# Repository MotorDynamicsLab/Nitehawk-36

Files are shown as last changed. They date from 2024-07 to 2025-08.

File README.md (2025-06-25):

# Nitehawk-36

Nitehawk-36 is a toolboard featuring RP2040 MCU, TMC2209 stepper drive, ADXL345 accelerometer, and USB port. Nitehawk-36's USB based connection method allows for a simple and easy setup compared to other CAN toolboards. The USB connnection also allows for a secondary USB port to connect your nozzle webcam or eddy current probe.

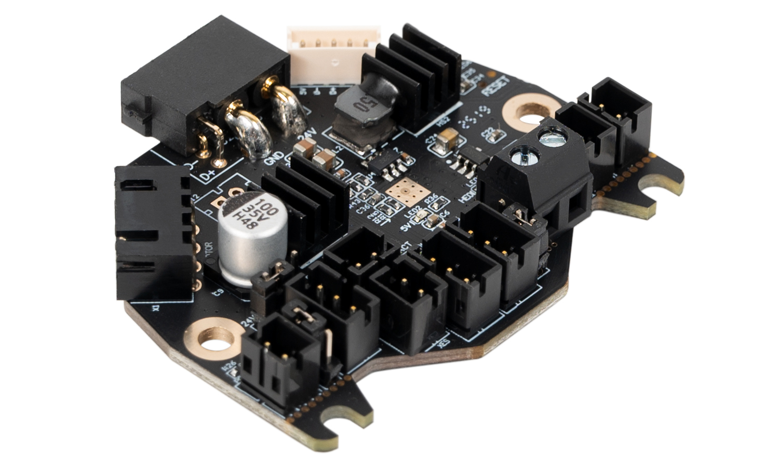
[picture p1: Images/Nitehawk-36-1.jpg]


# Features:

- Convenient wiring, no more complicated and error prone breakout cables
- USB Klipper connection, no additional software or hardware setup compared to CAN.
- Secondary USB port, an onboard USB port allows you to connect a second USB - device to your toolhead without running an additional umbilical cable.
- Custom toolhead cable, a single combined USB data and power cable rated for drag chain use, but can also be used in umbilical configuration.
- Convenient Input Shaping, run input shaper calibration at anytime with an onboard accelerometer.
- Tacho enabled HEF, the hotend fan port is three pin tachometer compatible, allowing for additional diagnostics and safety.

# Mount Guide
[Nitehawk 36 Universal Mount Guide](../master/STLs/Universal_Mount/NiteHawk%2036%20Mount.pdf)

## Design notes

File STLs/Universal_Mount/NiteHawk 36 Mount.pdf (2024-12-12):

# NiteHawk 36

## Universal Mount

# Mounts and Motor Adapter

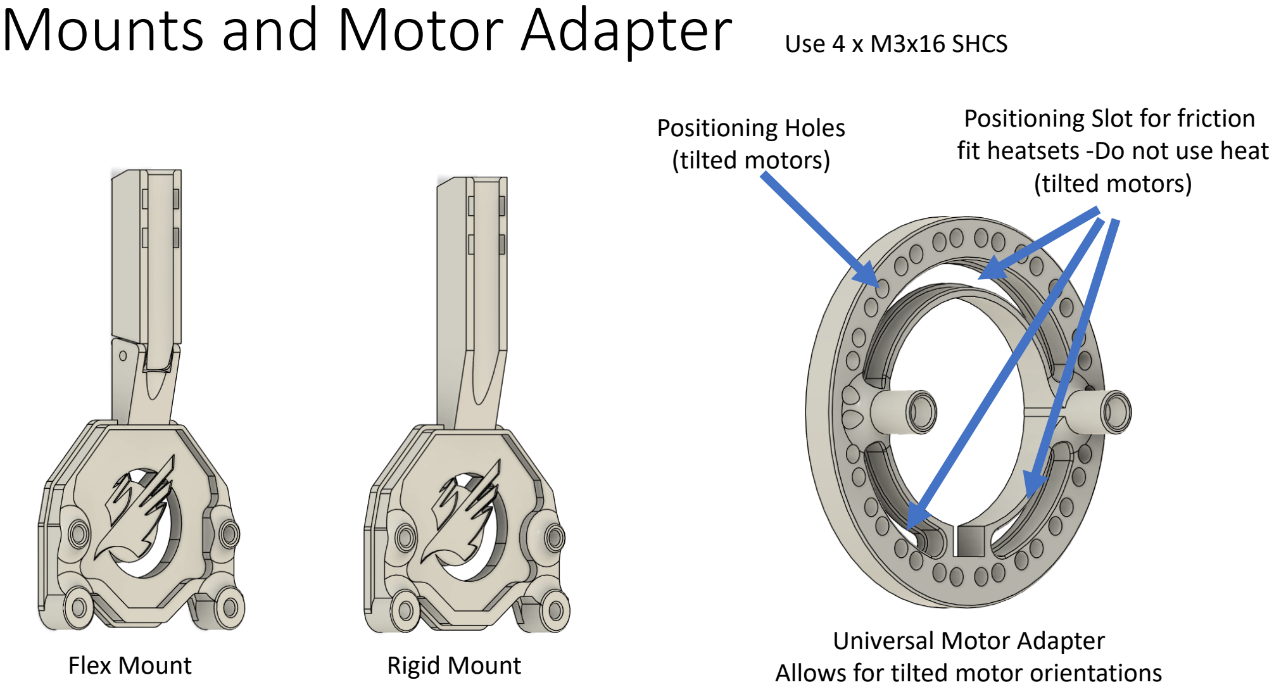
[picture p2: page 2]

Flex Mount | Rigid Mount

Universal Motor Adapter
Allows for tilted motor orientations

Positioning Slot for friction fit heatsets -Do not use heat (tilted motors)

Positioning Holes
(tilted motors)

Use 4 x M3x16 SHCS

# Flex Mount Prep

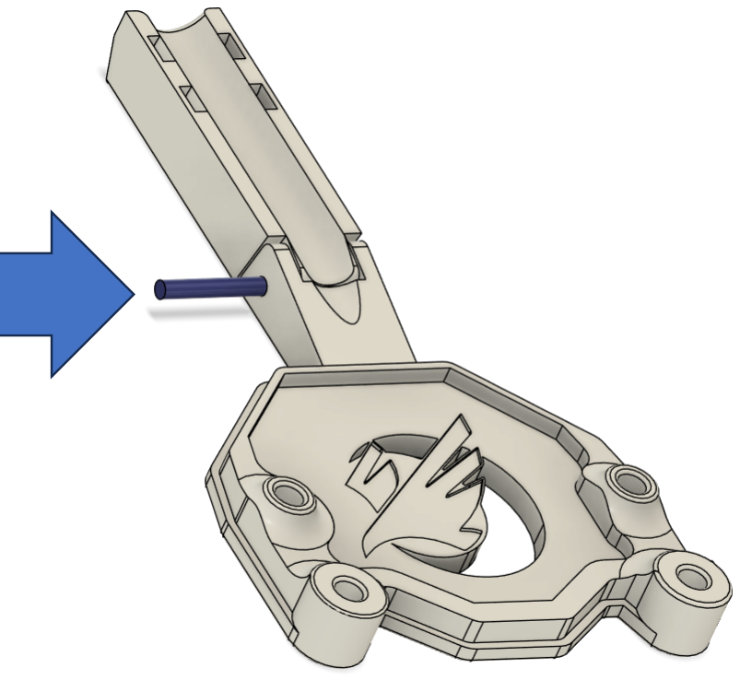
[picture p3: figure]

Cut a piece of filament slightly longer than the wide of the strain relief. Insert a piece of filament as a hinge. Melt the ends so the filament stay in place with a soldering iron.

# Flex and Rigid Mount Prep

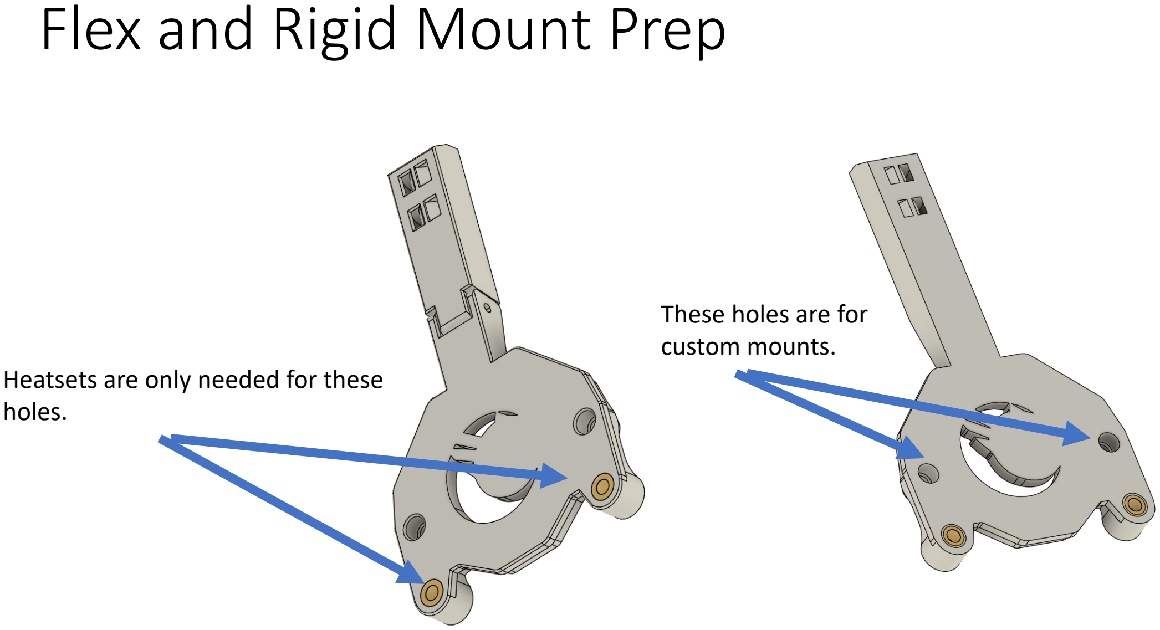
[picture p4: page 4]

Heatsets are only needed for these holes.

These holes are for
custom mounts.

# Extruders with Aligned Motor

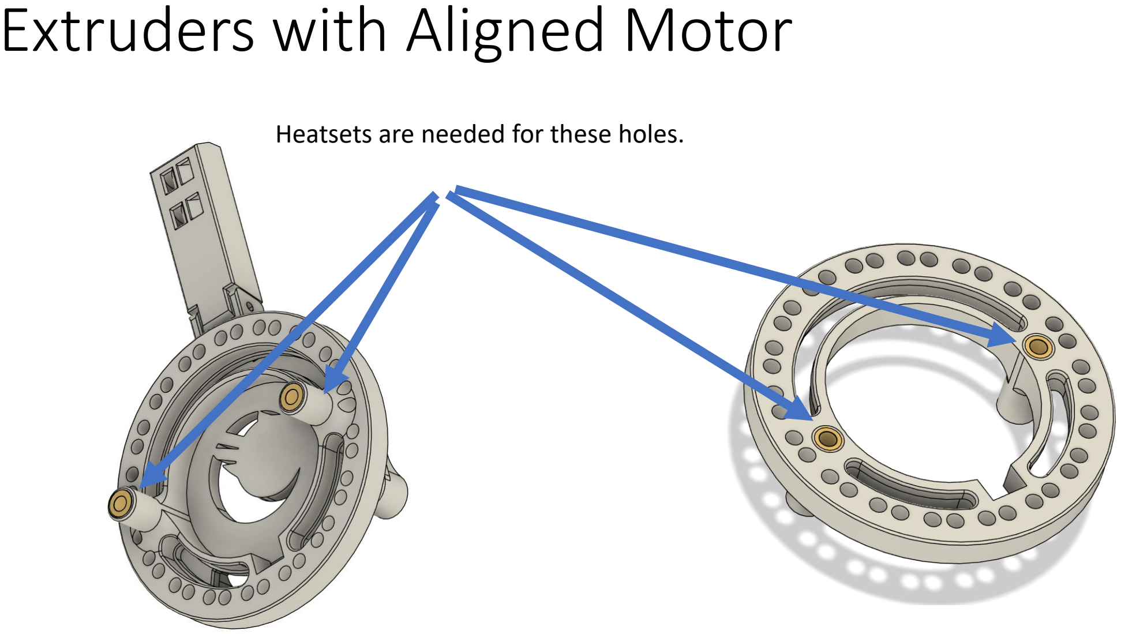
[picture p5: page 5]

Heatsets are needed for these holes.

# Extruders with Tilted Motor

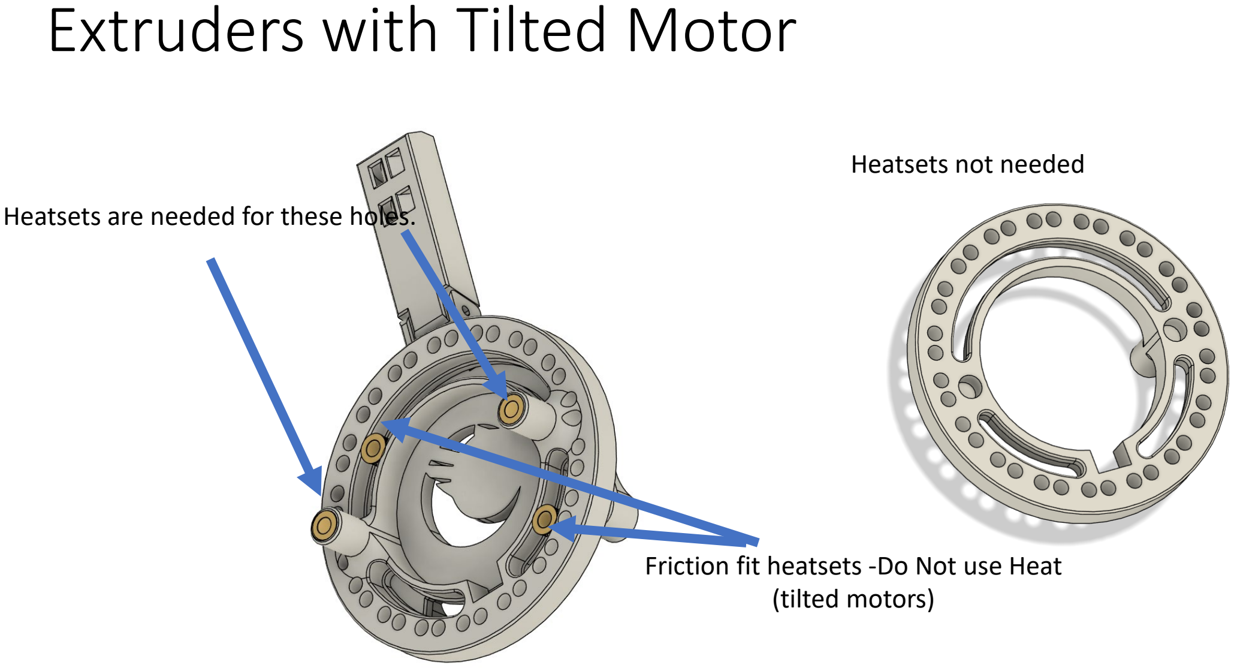
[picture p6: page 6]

Friction fit heatsets -Do Not use Heat (tilted motors)

Heatsets not needed
Heatsets are needed for these holes.

# Securing the NH36 Board

1. Use 2x M3x16 SHCS thread into plastic Do NOT overtighten

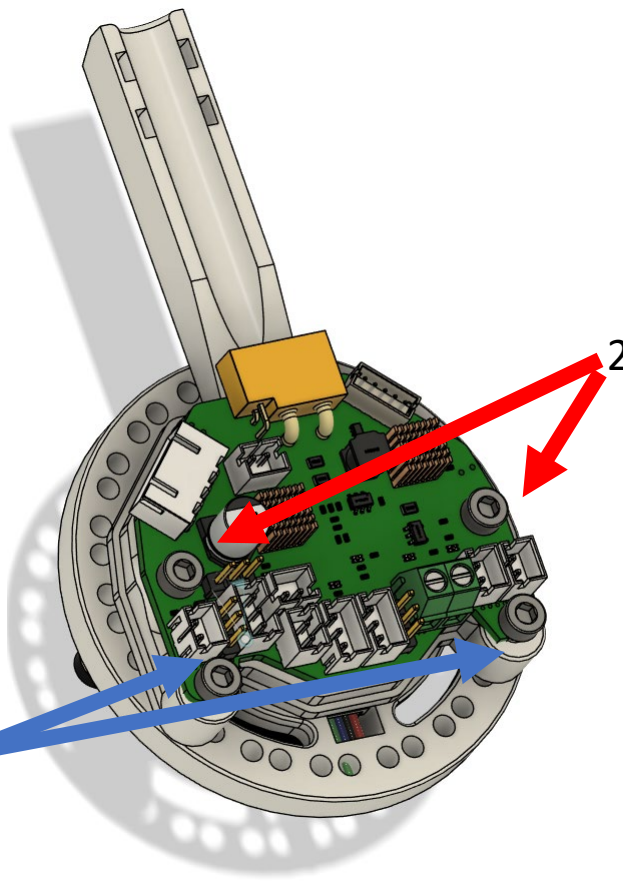
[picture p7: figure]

2.Use 2x M3x16 SHCS into friction fit heatsets

# Example

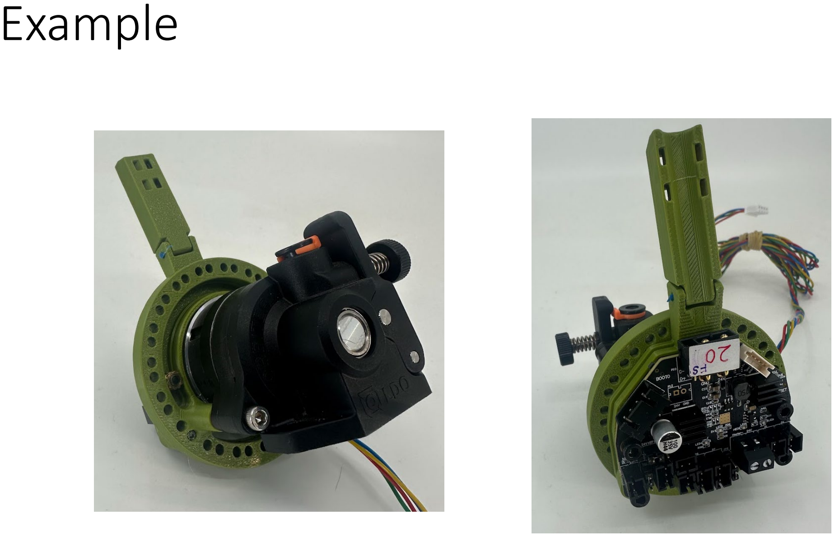
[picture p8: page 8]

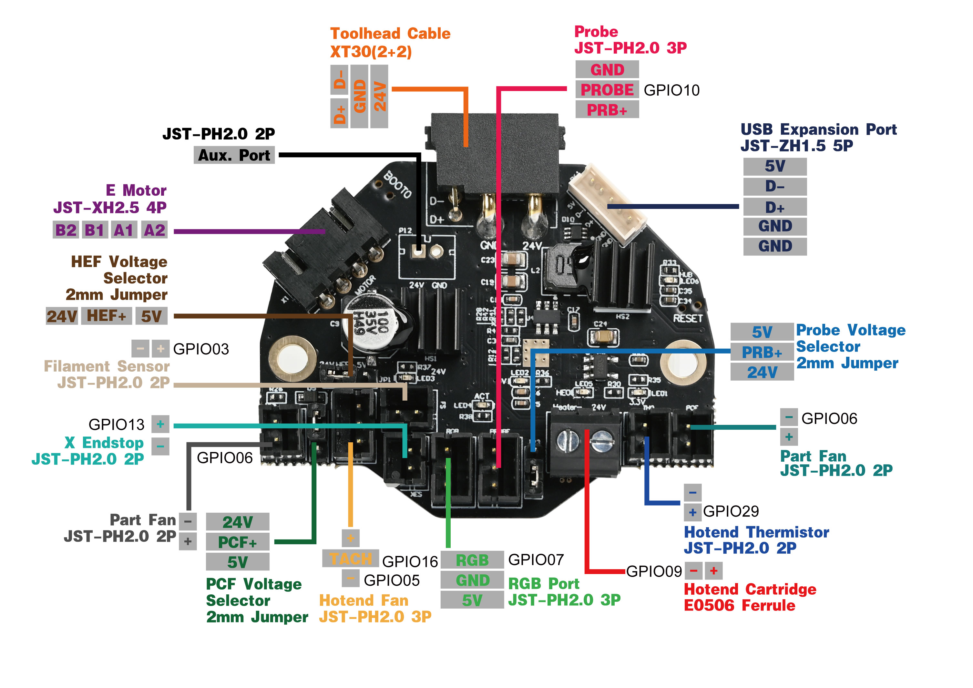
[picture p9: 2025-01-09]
Images/nh36_pcb_pinout.jpg

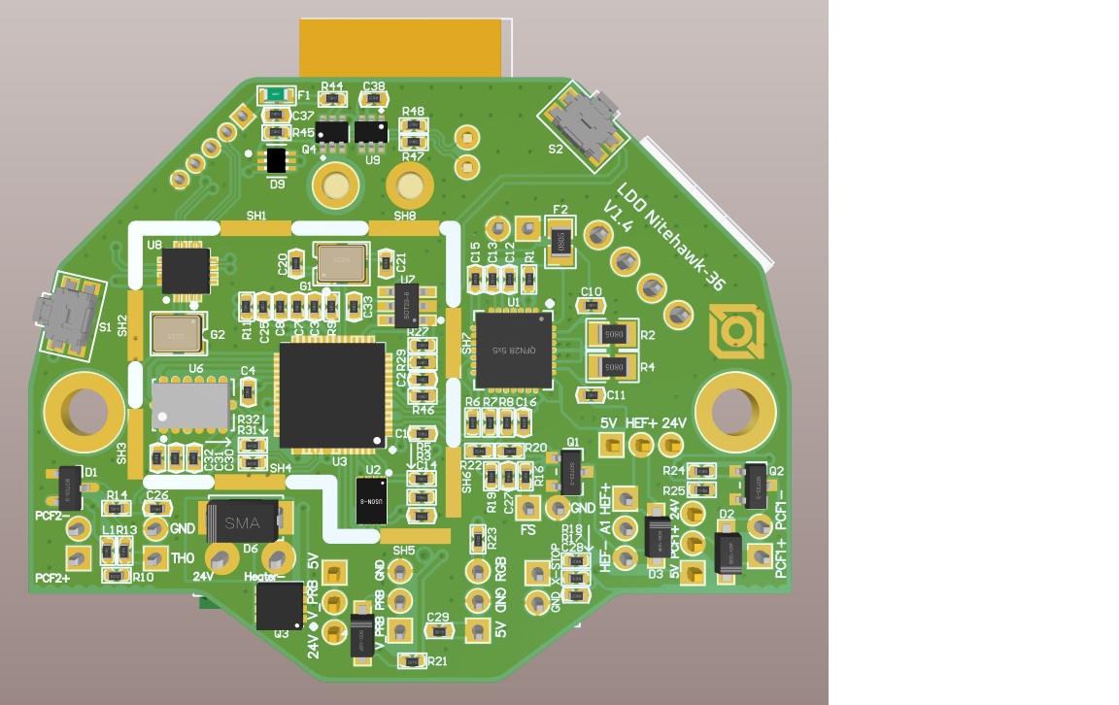
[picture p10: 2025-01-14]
Hardware/Nitehawk-36 V1.4/Nitehawk-36_V1.4 3D Layout Bottom.jpg

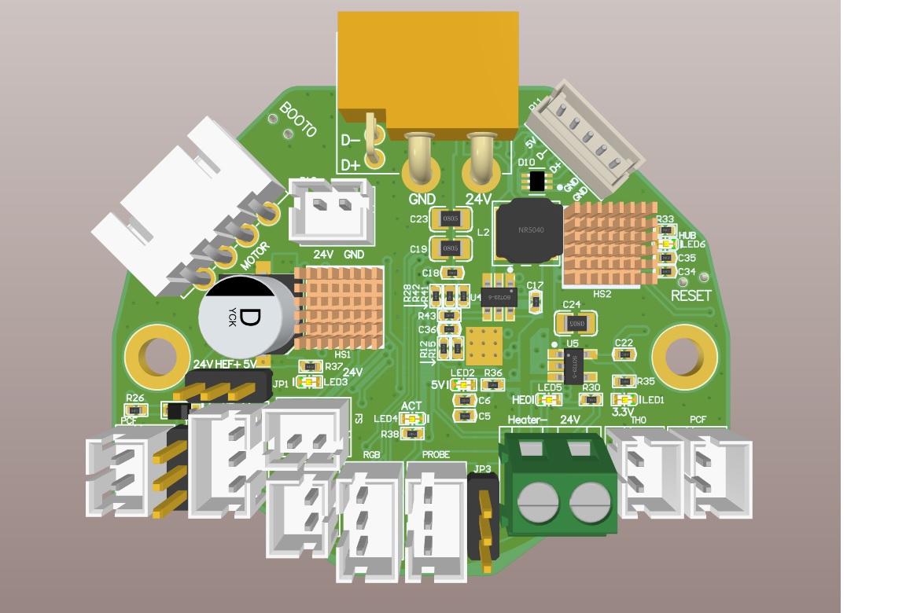
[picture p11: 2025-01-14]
Hardware/Nitehawk-36 V1.4/Nitehawk-36_V1.4 3D Layout Top.jpg

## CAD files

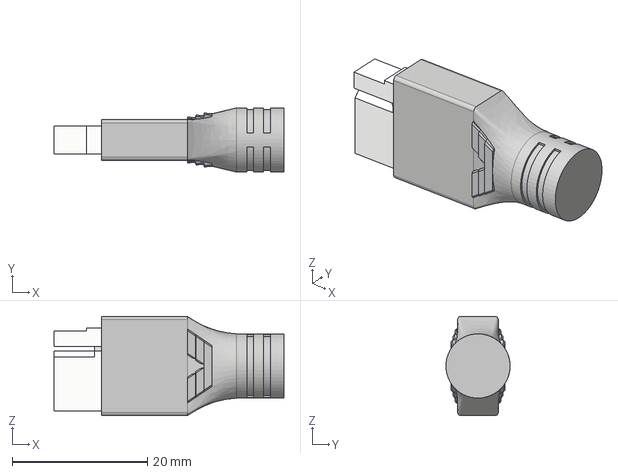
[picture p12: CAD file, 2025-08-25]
CAD/Umbilical_Overmold.step
34.0 x 9.50 x 14.7 mm
Connector
Overmold

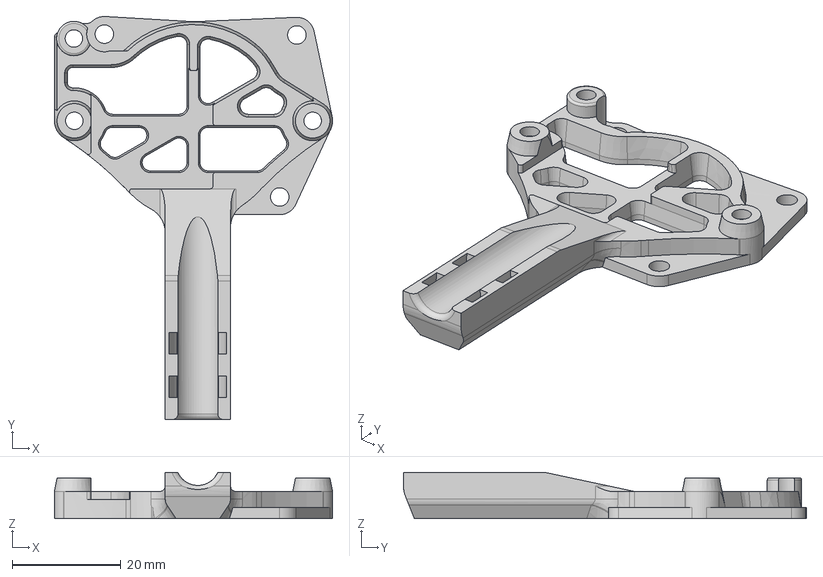
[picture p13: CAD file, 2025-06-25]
STLs/G2SA_WWG2_Mounts/NH36_v2_mount_WWG2.step
51.2 x 74.1 x 8.50 mm

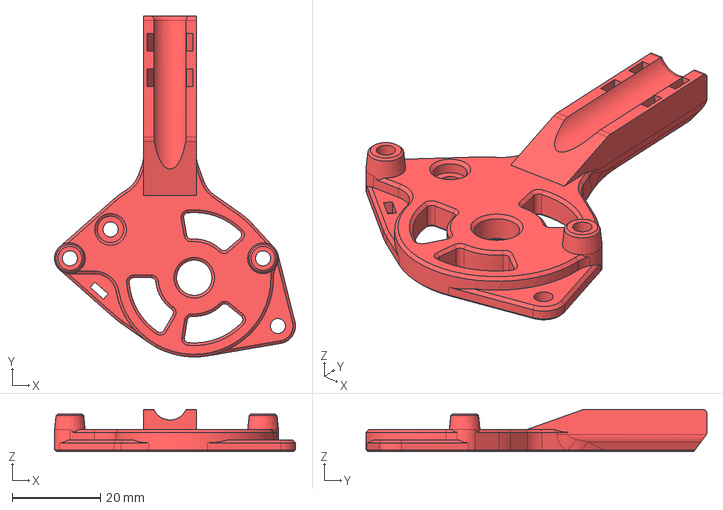
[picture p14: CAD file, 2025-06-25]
STLs/Generic_O2_Mount/NH36_O2_mount.step
54.7 x 77.4 x 9.60 mm

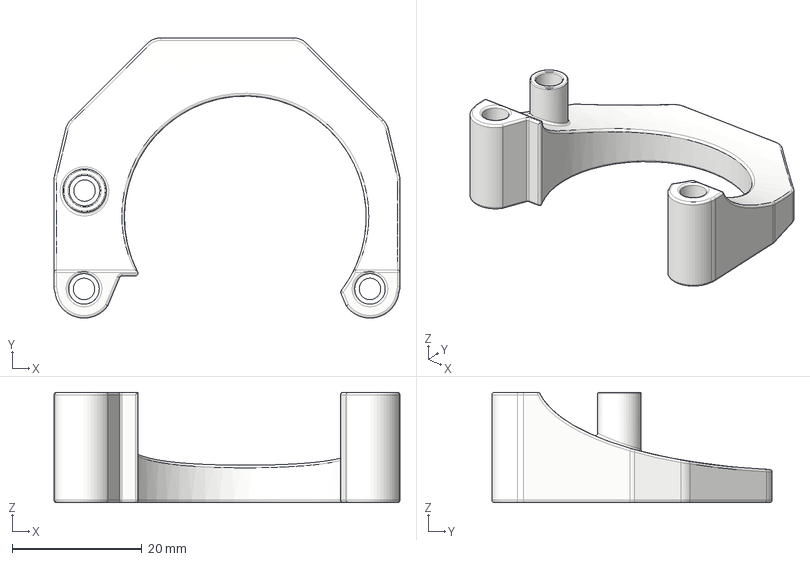
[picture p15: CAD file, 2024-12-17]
STLs/Universal_Mount/OrbiterMount.step
53.2 x 43.1 x 17.0 mm

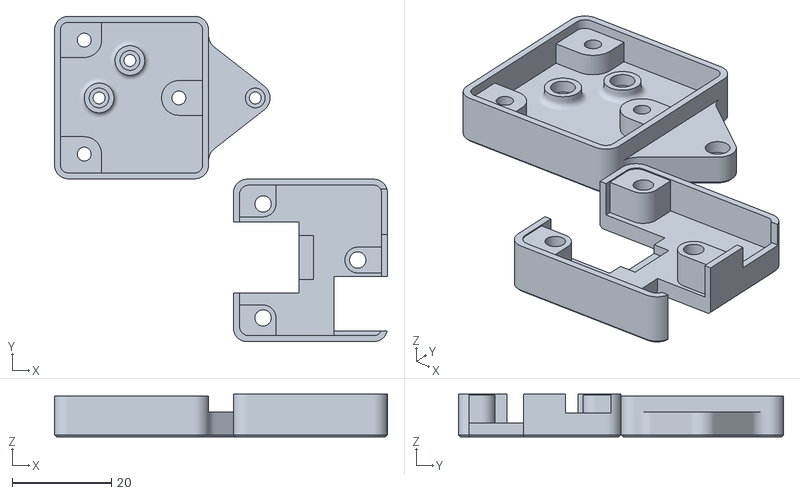
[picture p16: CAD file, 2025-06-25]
STLs/usb_adapter_mount_narrow.stl
67.2 x 65.6 x 8.60

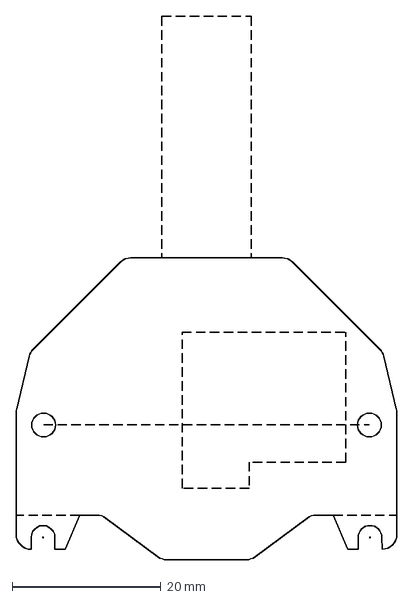
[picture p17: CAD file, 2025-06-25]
CAD/NH36-outline.dxf
51.2 x 73.1 mm

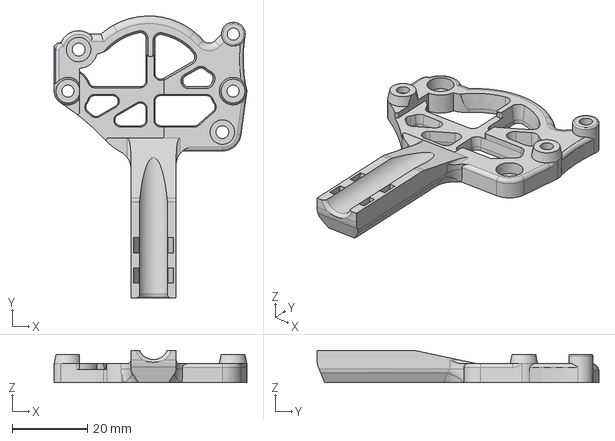
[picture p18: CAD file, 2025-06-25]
STLs/G2SA_WWG2_Mounts/NH36_v2_mount_G2SA.step
51.2 x 74.9 x 8.50 mm

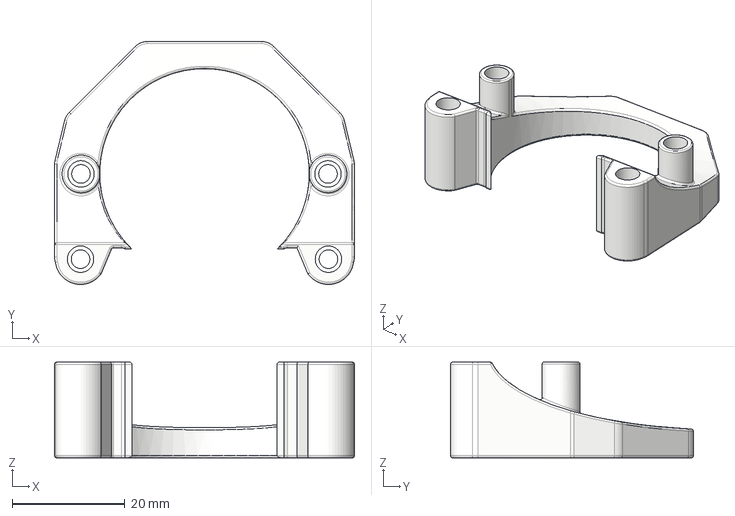
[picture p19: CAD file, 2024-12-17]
STLs/Universal_Mount/StandardMount.step
53.2 x 43.1 x 17.0 mm

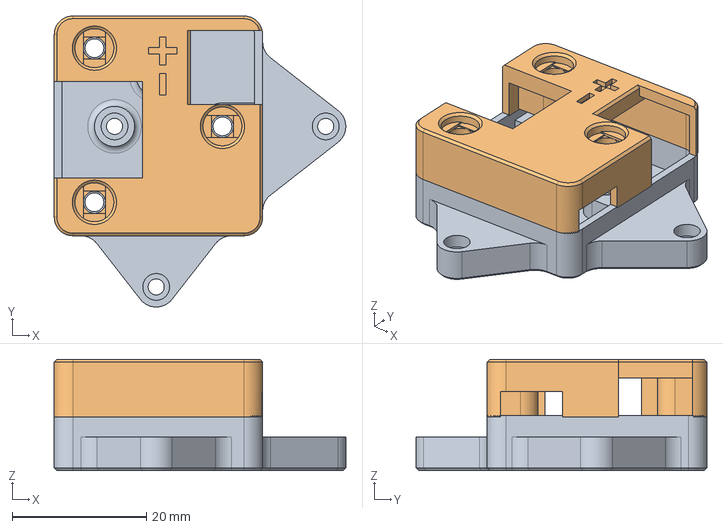
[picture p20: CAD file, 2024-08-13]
STLs/usb_adapter_mount.step
43.5 x 43.4 x 16.6 mm
Mount
Cover

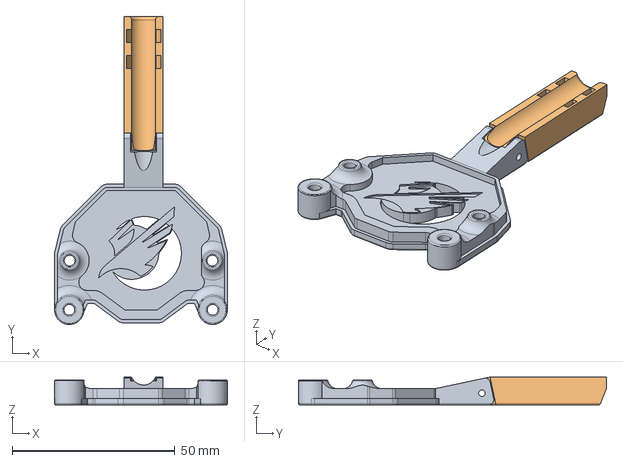
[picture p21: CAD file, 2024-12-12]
STLs/Universal_Mount/NH36_Flex_Mount.step
53.2 x 94.6 x 8.50 mm
Mount
Strain

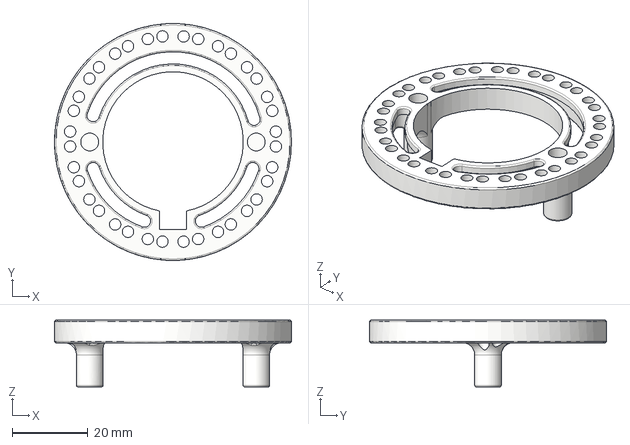
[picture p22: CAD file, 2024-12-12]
STLs/Universal_Mount/LDO36STH20Adapter.step
62.4 x 62.4 x 17.6 mm

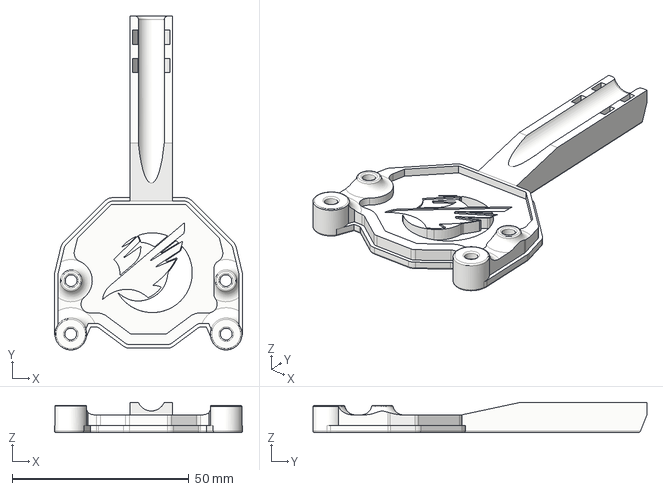
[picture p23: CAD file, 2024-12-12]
STLs/Universal_Mount/NH36_Rigid_Mount.step
53.2 x 94.6 x 8.50 mm

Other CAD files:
STLs/G2SA_WWG2_Mounts/NH36_v2_mount_G2SA.stl
STLs/G2SA_WWG2_Mounts/NH36_v2_mount_WWG2.stl
STLs/Generic_O2_Mount/NH36_O2_mount.stl
STLs/Universal_Mount/NH36_Flex_Mount.stl
STLs/Universal_Mount/NH36_Rigid_Mount.stl
STLs/Universal_Mount/OrbiterMount.stl
STLs/Universal_Mount/StandardMount.stl
STLs/usb_adapter_mount.stl

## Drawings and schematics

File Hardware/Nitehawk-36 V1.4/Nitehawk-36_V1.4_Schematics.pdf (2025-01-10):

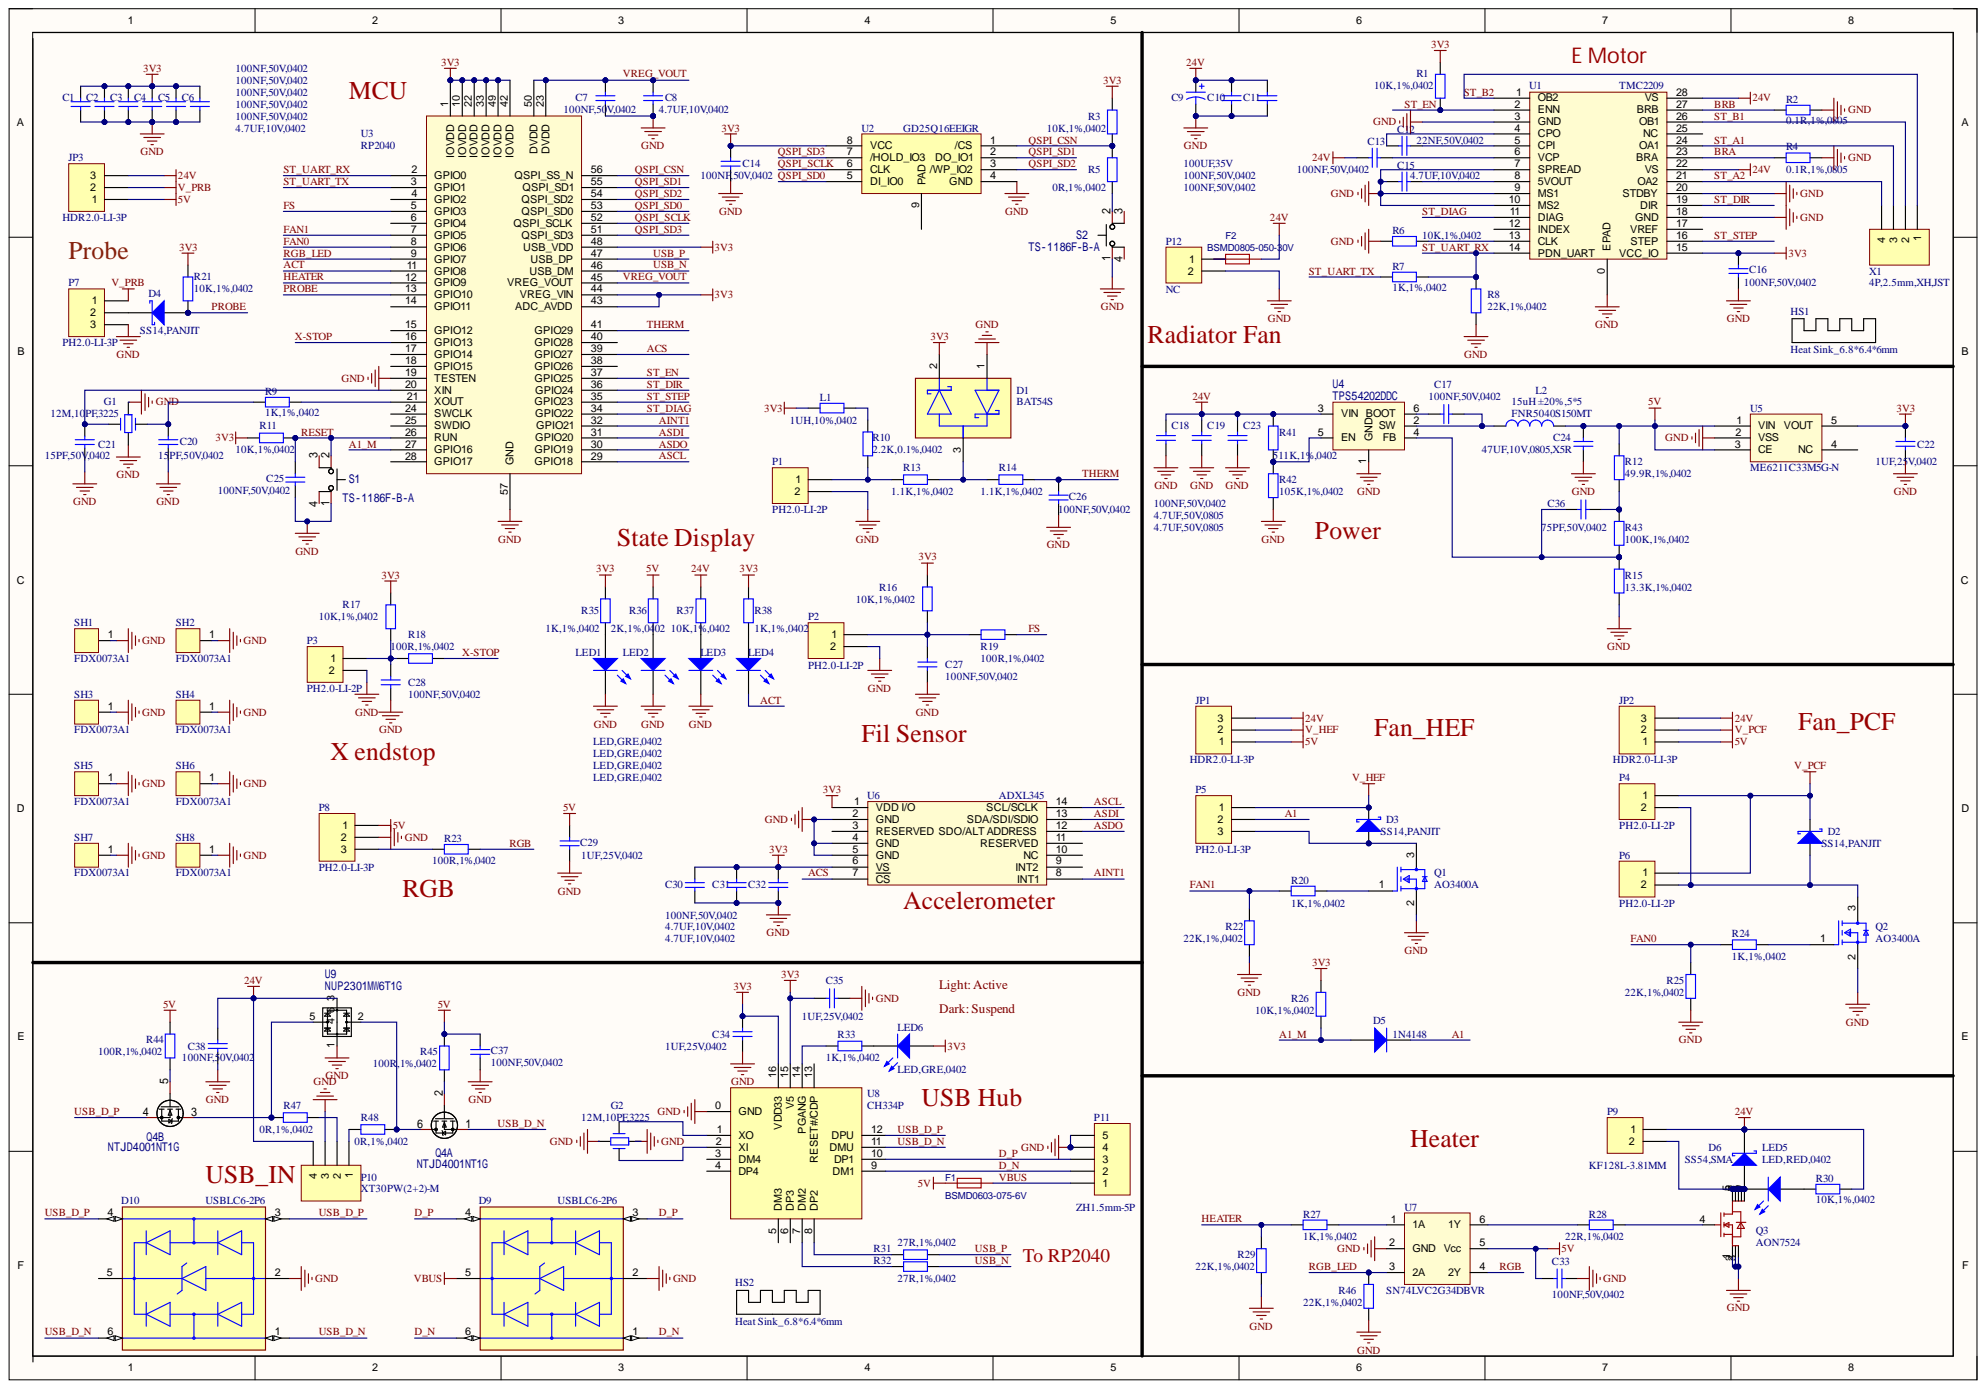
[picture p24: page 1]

XIN 20 | ST_DIR
XOUT 21

DM4 3
DP4 4 | D_N

F1 VBUS

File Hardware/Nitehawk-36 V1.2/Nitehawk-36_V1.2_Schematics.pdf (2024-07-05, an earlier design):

VCC_IO | 15 STEP | 16 VREF | 17 GND | 18 DIR | 19 STDBY | 20 OA2 | 21 VS | 22 BRA | 23 OA1 | 24 NC | 25 OB1 | 26 BRB | 27 VS | 28

# E Motor

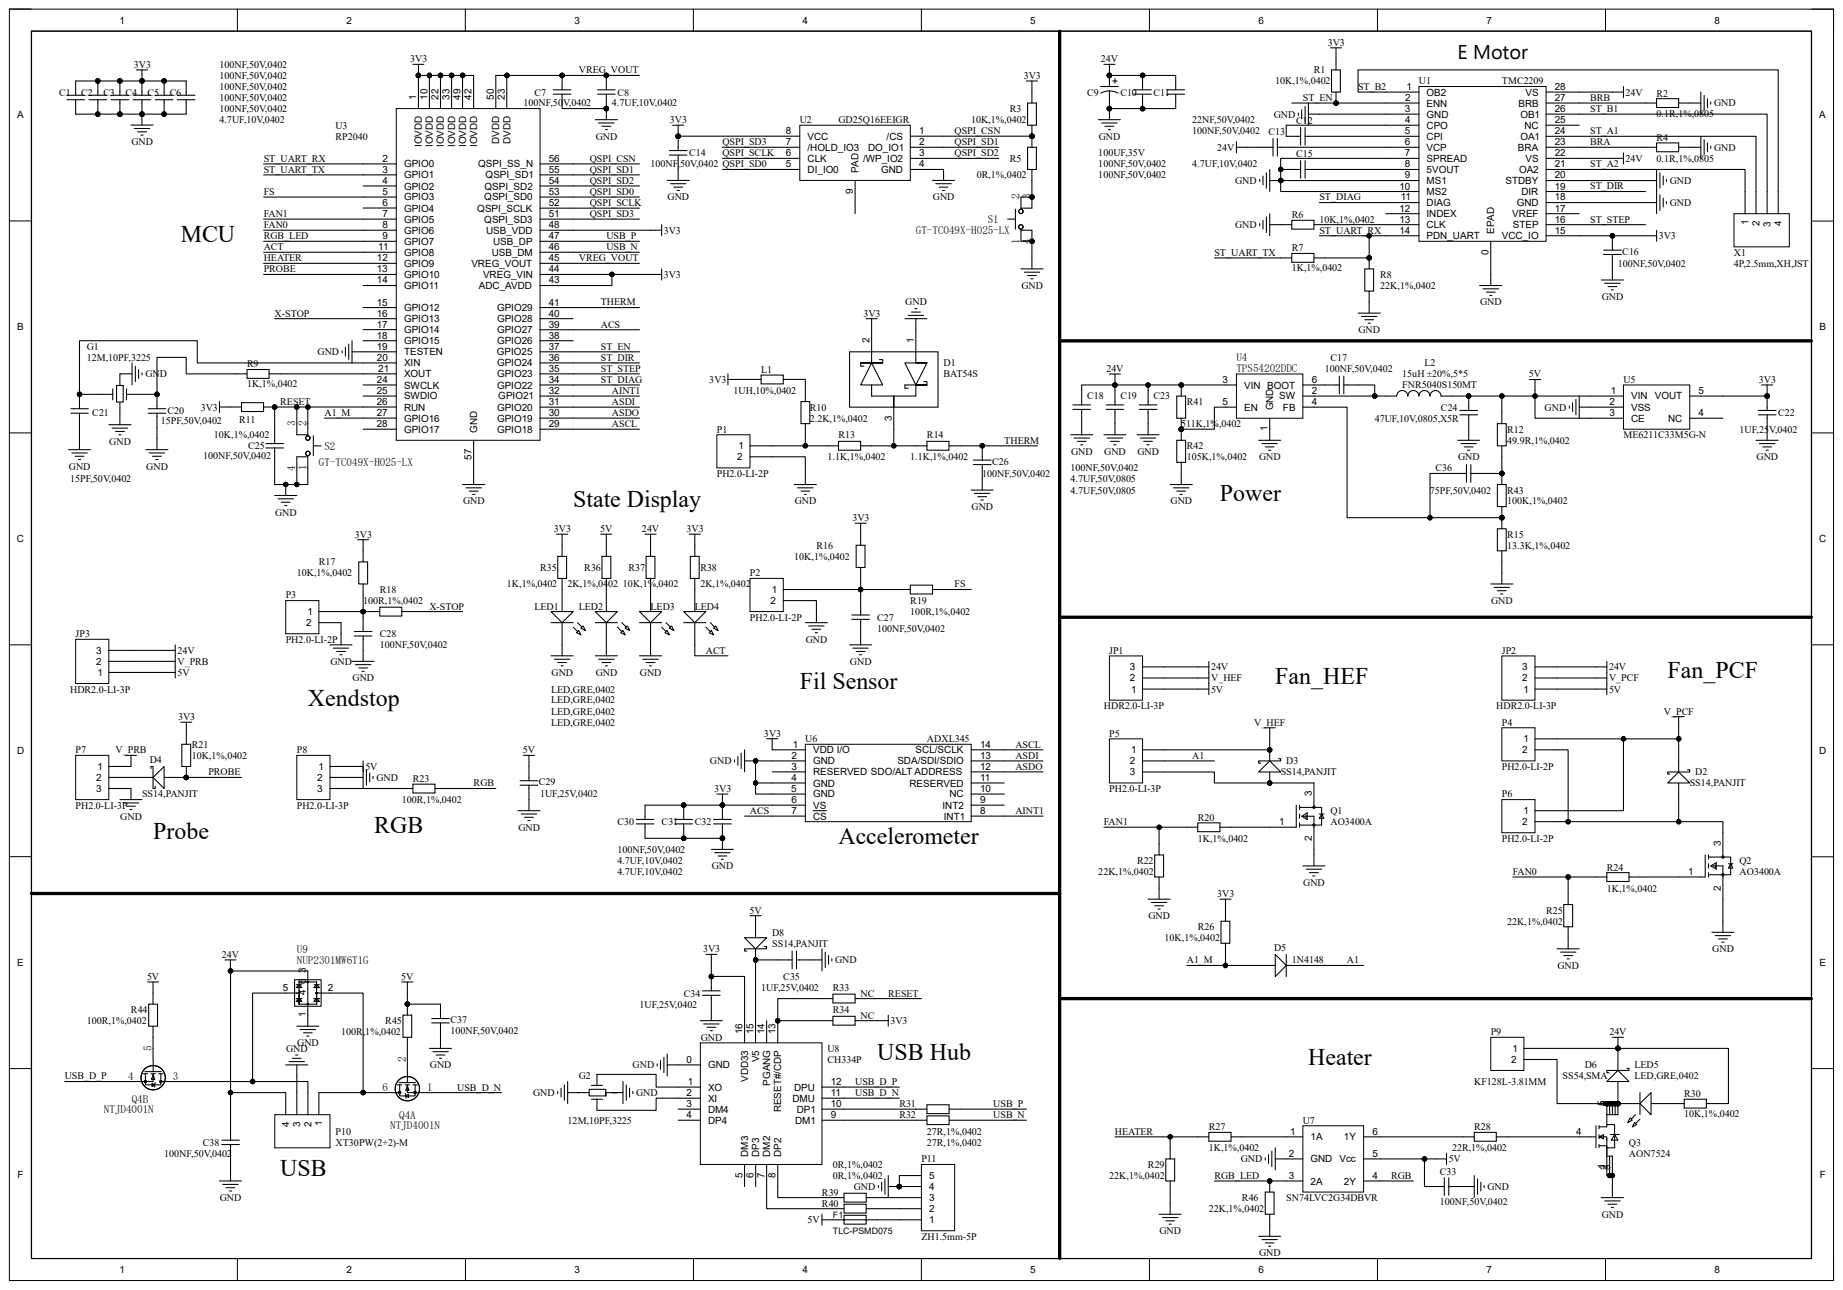
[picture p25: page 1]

ENN 2 | BRB
GND 3 | 0.1R,1%,0805 ST_A1

XIN 20 | ST_DIR
XOUT 21

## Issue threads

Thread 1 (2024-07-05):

STEP files for USB adaptor

YanceyA, 2024-07-05:
Hi, can you provide the STEP file for each top and bottom of the usb adaptor case? I would like to modify the wall thickness in a few areas to print properly with a 0.5mm nozzle.

The following areas are thin and do not slice well. Generally wall thickness should be 1mm to enable good slicing for most 3d printer settings.
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

camerony, 2024-08-13:
Step file added

Closed 2024-08-13.

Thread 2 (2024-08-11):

Error message during homing

printicus, 2024-08-11:
I have an NiteHawk 36 usb toolhead and i keep getting this error message:

"Error during homing probe: Communication timeout during homing"

I saw this message on different forums, but relatet to CANbus devices. Anny solution to resolve this?

My setup: Manta M8P with CB1.

reboot-8, 2025-06-20:
I am having the same issue as well. Although mine only happens after the first print. If I restart Klipper in between prints, it goes away until my second print in a row.

I am running a Fly Mellow Gemini v3 with a zero click probe on my V0

reboot-8, 2025-06-24:
I may have found a "fix" that seems to work.
I changed TRSYNC_TIMEOUT from 0.025 to 0.060 in /home/pi/klipper/klippy/mcu.py
https://forum.vorondesign.com/threads/error-communication-timeout-during-homing-probe-on-mellow-sb2040.1177/
Not sure how "hacky" this is, but so far seems to have fixed it for me. No issues so far in back to back prints.
YMMV.

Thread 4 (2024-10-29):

Include USB-Hub controller to the USB-Adapter Board

dermathes17, 2024-10-29:
An integrated 4 or 6 Port USB-Hub on the USB-Adapter PCB could be a solution for a more sophisticated wirering for toolchangers like the Stealthchanger.

gyscos, 2024-10-31:
You may be interested in https://github.com/xbst/Birds-Nest

Closed 2025-05-13.

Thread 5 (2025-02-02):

chamber thermistor

ericderace, 2025-02-02:
Is there any port on the nitehawk-36 where one could connect a chamber thermistor, much like on the nitehawk-sb?

cneshi, 2025-05-13:
unfortunately the current version of NH-36 does not have the extra thermistor port like SB has. There simply was not enough space

Closed 2025-05-13.

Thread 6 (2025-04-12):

Is it possible to use a BL Touch or Microprobe V2 with the Nitehawk 36 ?

midicdj1000, 2025-04-12:
HI,
I am upgrading an old ender 3 max with Klipper and decided to give the Nitehawk 36 a go, but I can't find a way to use a BL touch or BIQU Microprobe v2 (this is what I have)  type probe. I can see it has a Probe port that can be set to 5v, but not sure if this would work and I think it is made to be used with inductive probes ?

Daisy1819, 2025-04-22:
Hi, the NH36 indeed has the 5V probe.

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

cneshi, 2025-05-13:
For BLtouch type probes, you need an additional output signal to command the probe to extend outwards. Since the probe port only has single input signal, you might need to use an additional pin from another unused port for the output signal (perhaps X endstop or Filament sensor)

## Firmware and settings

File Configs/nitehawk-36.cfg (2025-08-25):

# This file contains pin mappings for the LDO Nitehawk-36 Toolboard
# To use this config, the firmware should be compiled for the Raspberry Pi RP2040
# Make sure to include this config *at the end* of printer.cfg to overwrite the relevent sections

# See https://docs.ldomotors.com/en/Toolboard/nitehawk-36#firmware-setup-and-update
# For instructions on uploading/updating klipper firmware to the PCB

## LDO Nitehawk-SB Toolboard Partial Config

## *** THINGS TO CHANGE/CHECK: ***
## MCU paths                            [mcu] section
## Thermistor types                     [extruder] sections

## *MAKE SURE* to include this partial config file *AFTER* the main controller config. 
## This will ensure the relavent sections are overwritten by the pin mappings specified here.

[mcu nhk]
##  Obtain definition by "ls -l /dev/serial/by-id/" then unplug to verify
##--------------------------------------------------------------------
serial: /dev/serial/by-id/usb-Klipper_rp2040_E012345678900000-if00
restart_method: command
##--------------------------------------------------------------------

#####################################################################
#   Endstops
#####################################################################
## XES - Toolhead PCB
[stepper_x]
endstop_pin: nhk:gpio13


#####################################################################
#   Filament Sensor
#####################################################################
#[filament_switch_sensor filament_sensor]
#switch_pin: nhk:gpio3
#pause_on_runout: True

#####################################################################
# 	Extruder
#####################################################################
[extruder]
step_pin: nhk:gpio23
dir_pin: nhk:gpio24
enable_pin: !nhk:gpio25
heater_pin: nhk:gpio9
sensor_pin: nhk:gpio29
pullup_resistor: 2200

[tmc2209 extruder]
sense_resistor: 0.100
uart_pin: nhk:gpio0
tx_pin: nhk:gpio1
interpolate: false
#run_current:         #recommend setting it below 0.7A.

#####################################################################
#   Fans
#####################################################################
## PCF
[fan]
pin: nhk:gpio6


## HEF
[heater_fan hotend_fan]
pin: nhk:gpio5
tachometer_pin: nhk:gpio16
tachometer_ppr: 2

#####################################################################
# 	Probe
#####################################################################
## Probe Port
[probe]
pin: nhk:gpio10

#####################################################################
#   Lights
#####################################################################
##Stealthburner Headlights
[neopixel sb_leds]
pin: nhk:gpio7
chain_count: 3
color_order: GRBW
initial_RED: 0.0
initial_GREEN: 0.0
initial_BLUE: 1.0
initial_WHITE: 0.0

## PCB Activity Light
[output_pin act_led]
pin: !nhk:gpio8

#####################################################################
#   Accelerometer
#####################################################################
[adxl345]
cs_pin: nhk:gpio27
spi_software_sclk_pin: nhk:gpio18
spi_software_mosi_pin: nhk:gpio20
spi_software_miso_pin: nhk:gpio19

[resonance_tester]
accel_chip: adxl345
accel_per_hz: 100
sweeping_accel: 400
sweeping_period: 0
##--------------------------------------------------------------------
## Uncomment below for 250mm build
#probe_points:
#    125, 125, 20

## Uncomment below for 300mm build
#probe_points:
#    155, 155, 20

## Uncomment below for 350mm build
#probe_points:
#    175, 175, 20

#####################################################################
#   Addtional Sensors
#####################################################################
[temperature_sensor NH36]
sensor_type: temperature_mcu
sensor_mcu: nhk
min_temp: 0
max_temp: 100

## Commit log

2024-06-07 add hardware files and klipper configure
    [nitehawk-36.cfg]
2024-06-12 add PCB pinout diagrams
2024-06-19 add filament_sensor
    [nitehawk-36.cfg]
2024-06-19 add tacho_macros.cfg file
    [tacho_macros.cfg]
2024-06-21 add stl file
    [usb_adapter_mount.stl]
2024-06-21 update nitehawk-36
    [nitehawk-36.cfg]
2024-06-24 add schematics
2024-07-09 added GPIO for filament sensor and X endstop
2024-07-17 revise pins of filament sensor and X endstop
2024-10-18 Add current configuration
    [nitehawk-36.cfg]
2024-12-12 NH36 Universal Mount
    [LDO36STH20Adapter.step, NH36_Flex_Mount.step, NH36_Flex_Mount.stl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]
2025-01-04 fix duplicate filament sensor config issue with Configs/nitehawk-36.cfg
    [nitehawk-36.cfg]
2025-01-15 Move universal mount to its own directory
    [LDO36STH20Adapter.step, NH36_Flex_Mount.step, NH36_Flex_Mount.stl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]
2025-01-15 move STP models to CAD directory
    [NH36-outline.dxf]
2025-01-15 upload generic O2 mount
    [NH36_O2_mount.step, NH36_O2_mount.stl]
2025-01-16 rename directories for O2 and Universal Mounts
    [LDO36STH20Adapter.step, NH36_Flex_Mount.step, NH36_Flex_Mount.stl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]
2025-01-16 add WWG2 and G2SA mounts from Blamm
    [NH36_v2_mount_G2SA.step, NH36_v2_mount_G2SA.stl, NH36_v2_mount_WWG2.step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]
2025-02-24 Add temperature sensor configuration to nitehawk-36.cfg
    [nitehawk-36.cfg]
2025-04-23 Add STLs/usb_adapter_mount_narrow.stl
    [usb_adapter_mount_narrow.stl]
2025-05-19 This macro only detects the PCF and is not valid in the nhk36 boards
    [tacho_macros.cfg]
2025-08-25 disable `sweeping` in `resonance_tester` section of config
    [nitehawk-36.cfg]
2025-08-25 add CAD model for umbilical overmold
    [Umbilical_Overmold.step]
